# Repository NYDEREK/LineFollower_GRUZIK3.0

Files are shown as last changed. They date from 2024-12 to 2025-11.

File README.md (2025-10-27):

<h1 align="center">GRUZIK3.0: Line Follower Robot</h1>

<div align="center">

   

<i>Loved the project? Please consider giving a Star ⭐️</i>

</div>

> **GRUZIK2.0 is a lightweight construction (69g) designed for the "Line Follower Light" competition. The robot features Bluetooth communication with a smartphone app and uses a digital sensor instead of analog.**

> **here is a quick video of current progres with GRUZIK3.0 - https://www.youtube.com/watch?v=DpuIcFJMwbQ**
<div align="center">
  
</div>

## Hardware

> **The simple lightweight construction (69g) allows the robot to achieve high speed on the track.**
> **PCBs were designed in KiCAD 8.0 and manufactured by JLCPCB. The rims were 3D printed with PLA for Kyosho "Mini Z" tires.**
> **The light dualsky 150mAh battery provides enough current (max 30C) without adding too much weight (10g).**
> **The Pololu 2211 motor (10:1) with max current 1.6A per one requires the use of two separate TB6612FNG motor drivers with connected channels (max 2A per driver).**
> **The HC-05 Bluetooth module gives communication range up to 10m.**
> **The fast ARM microcontroller STM32G474RET6 (max 170MHz) provides a lot of software capabilities.**

- uC - STM32G474RET6
- drivers - TB6612FNG
- sensor - 12x KTIR0711S
- battery - 150mAh LiPo dualsky
- wheels - Kyosho Mini Z
- motors - Pololu 3071 HPCB
- Bluetooth - HC-04
- Encoders - AMS AS5047P-ATSM
- IMU - MPU-6050

## 🗺️ Mapping 🗺️
> **GRUZIK3.0 is able to record it's route and save it on uSD card. Results can be represented as XY map and optimized by Python algorithm, robot is able to recreate optimized map in real world achieving max speed for the given route**

<div align="center">

</div>

## 📱Bluetooth Apps 📱

> **Thease are simple Bluetooth apps created with MIT App Inventor. Spps start and stop the robot. The Modes pad is responsible for quickly adapting the speed and accuracy of the robot to the route using modes, and the application also displays the battery charge status. Second app is mainly for tweaking PID settings it allows you to change any parameter in seconds**

<div align="center">
  
  
</div>

## What I have learned 
> **This project wasn't easy but I learned a lot new things in software and hardware. I had a lot of failures during this project but I have never gave up and always kept pushing my own limits.**

- I mastered PID controll
 
- IMU implemantation 
 
- Encoder implementation with PI speed regulator on motors
 
- Mapping and optimizing Paths

- Improved my PCB design skills (KiCAD)

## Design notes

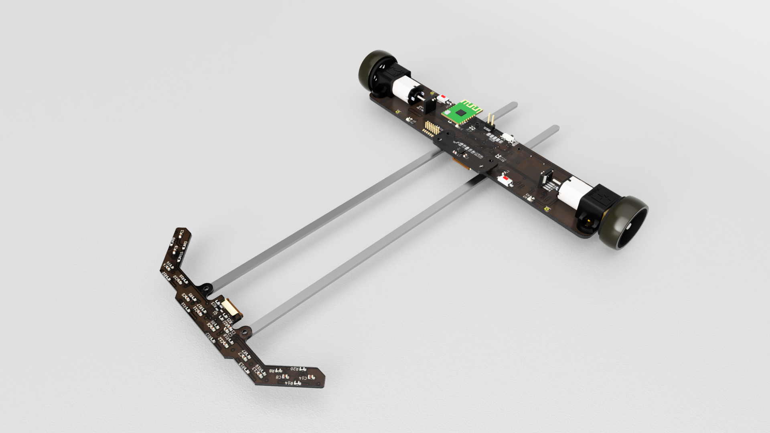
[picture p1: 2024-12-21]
Hardware/Renders/GRUZIK3.0_2024-Nov-24_09-44-59PM-000_CustomizedView13733252643_png.png

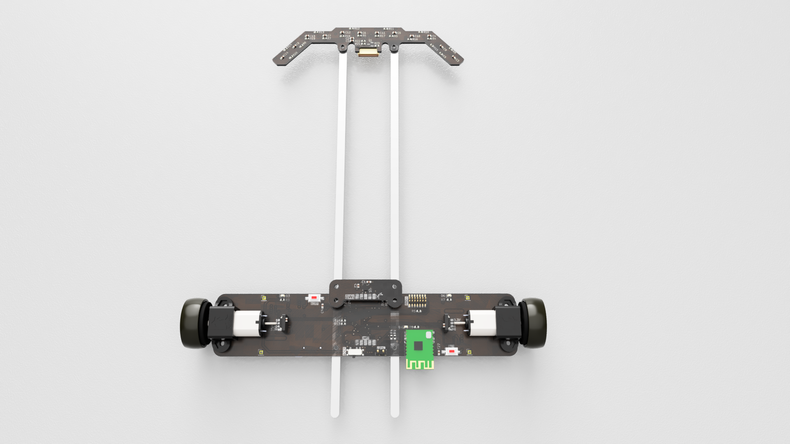
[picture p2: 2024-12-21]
Hardware/Renders/GRUZIK3.0_2024-Nov-24_10-15-36PM-000_CustomizedView15571638885_png.png

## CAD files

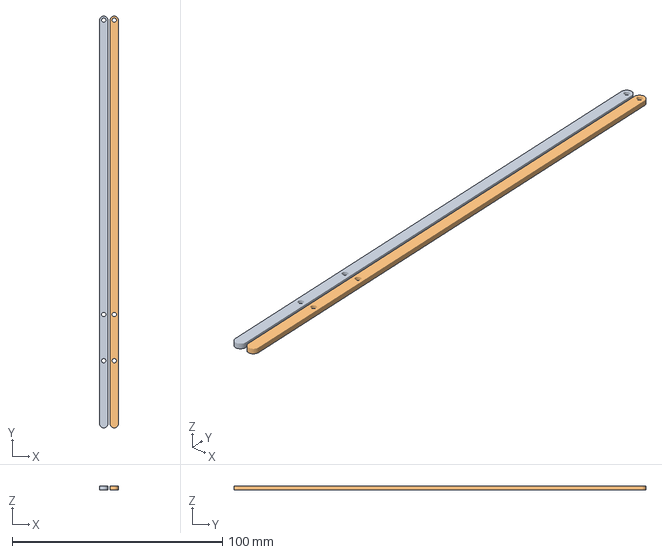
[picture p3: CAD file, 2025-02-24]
Hardware/3D Files/Board-Sensor-Connector/Connector.3mf
9.00 x 196.0 x 1.80 mm
Bryła1.stl x 2

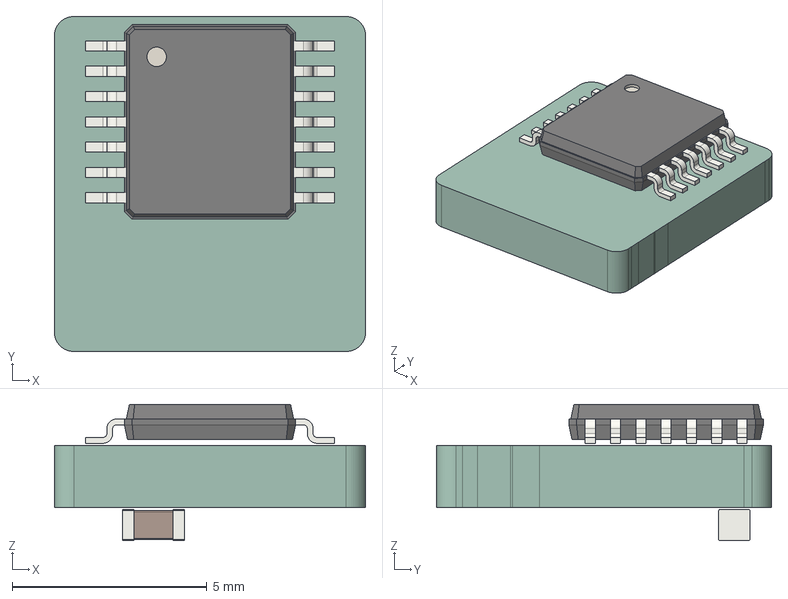
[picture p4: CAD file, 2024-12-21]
Hardware/3D Files/Encoder_3D_Files/Encoder_PCB.step
8.00 x 8.61 x 3.50 mm
TSSOP_14_44x5mm_P065mm
C_0603_1608Metric
Encoder_PCB_PCB

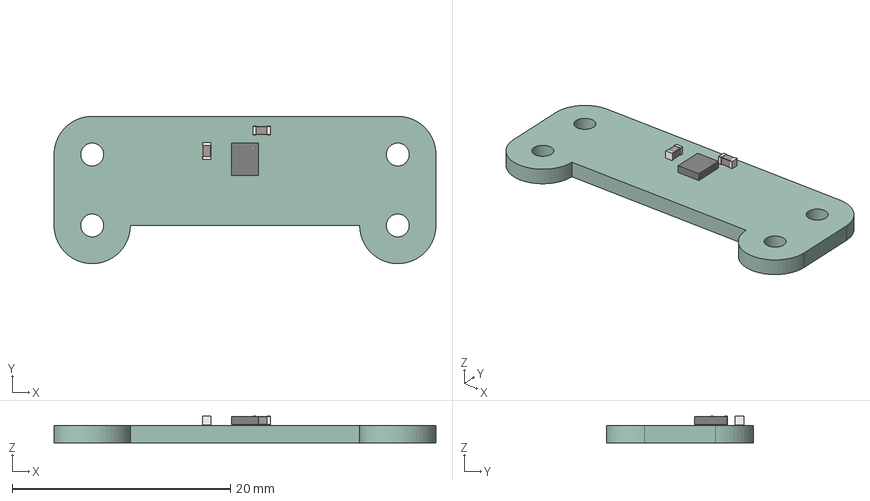
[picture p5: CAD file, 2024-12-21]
Hardware/3D Files/IMU_3D_Files/IMU_PCB.step
35.0 x 13.5 x 2.45 mm
LGA_14_3x25mm_P05mm_LayoutBorder3x4y
C_0603_1608Metric x 2
IMU_PCB_PCB

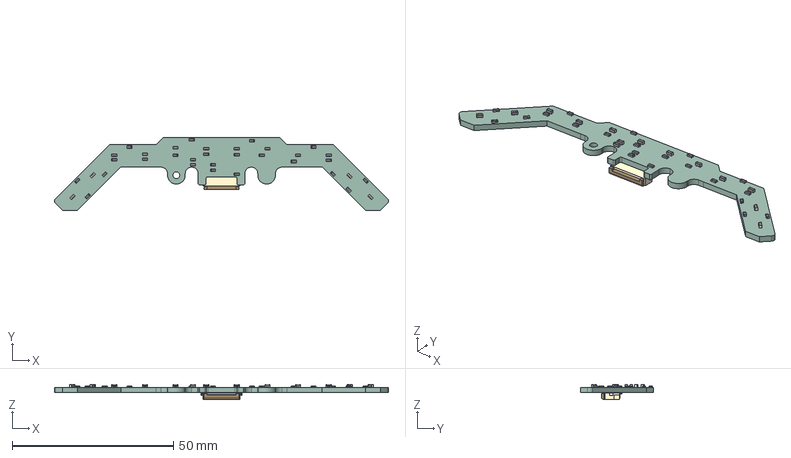
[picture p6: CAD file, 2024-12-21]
Hardware/3D Files/Sensor_3D_Files/Sensor_PCB.step
103.6 x 22.8 x 4.50 mm
C_0603_1608Metric x 14
R_0603_1608Metric x 21
Hirose_FH12_xxS_0_5SH_Parametric_v0_1
Sensor_PCB_PCB

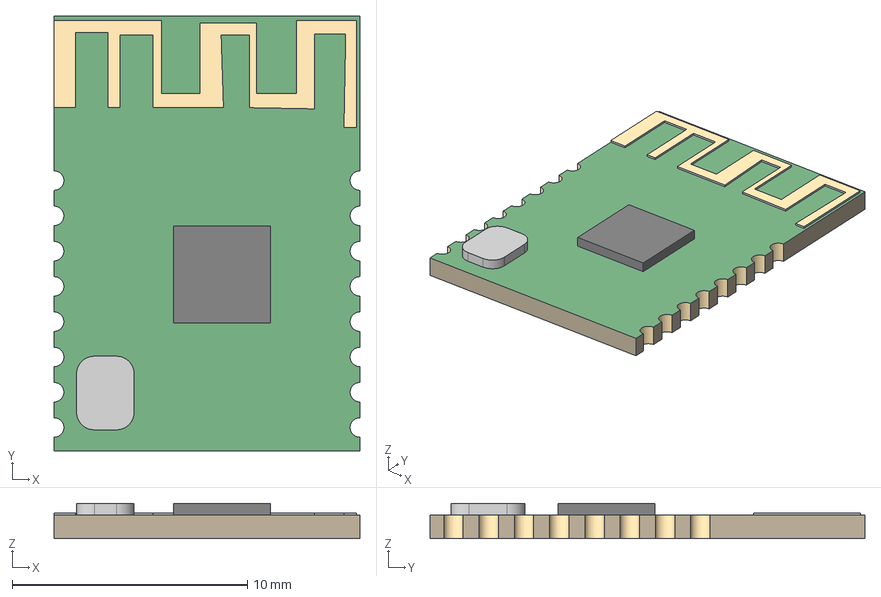
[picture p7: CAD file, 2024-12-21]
Hardware/PCB/KiCad project/Main_PCB_LF_3.0/Main_PCB_GRUZIK_3.0/HC-04/3D model/HC-04 v2.step
13.0 x 18.5 x 1.50 mm

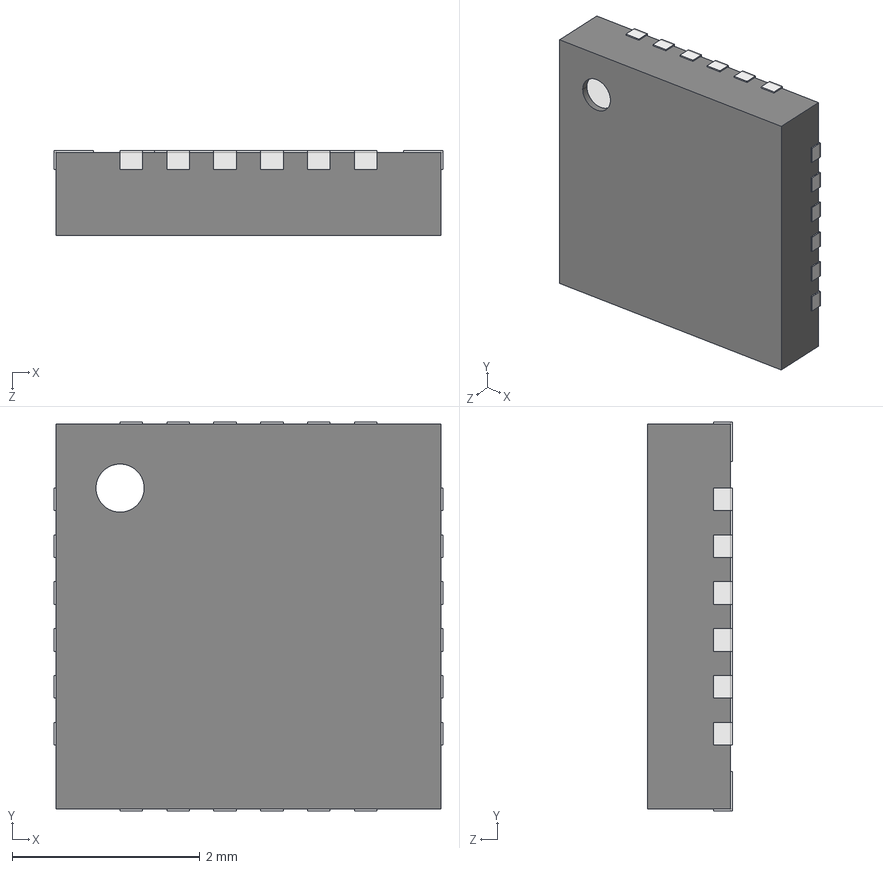
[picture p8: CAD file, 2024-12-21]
Hardware/PCB/KiCad project/Main_PCB_LF_3.0/Main_PCB_GRUZIK_3.0/MPU6050_3D_model/QFN 24.STEP
4.14 x 4.14 x 0.9 mm
Open_CASCADE_STEP_translator_6.8_11.2.1.step_Varsay考an
Open_CASCADE_STEP_translator_6.8_11.4.1.step_Varsay考an x 24
Open_CASCADE_STEP_translator_6.8_11.1.step_Varsay考an
Thermal_Shape.step_Varsay考an

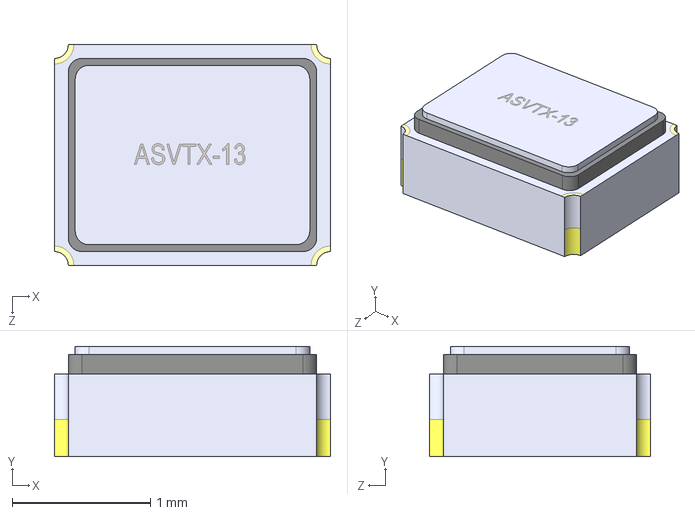
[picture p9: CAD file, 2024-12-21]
Hardware/PCB/KiCad project/Main_PCB_LF_3.0/Main_PCB_GRUZIK_3.0/X1_3D_model/ASVTX-13.STEP
2.00 x 0.8 x 1.60 mm

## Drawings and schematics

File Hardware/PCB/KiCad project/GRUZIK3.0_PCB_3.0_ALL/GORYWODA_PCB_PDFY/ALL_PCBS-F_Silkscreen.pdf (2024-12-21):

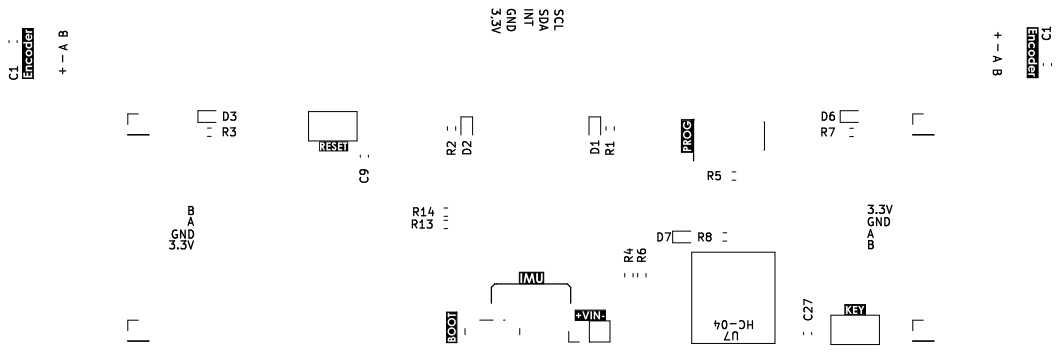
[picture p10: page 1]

GND SDA B B 3,3V INT SCL A GND AGND

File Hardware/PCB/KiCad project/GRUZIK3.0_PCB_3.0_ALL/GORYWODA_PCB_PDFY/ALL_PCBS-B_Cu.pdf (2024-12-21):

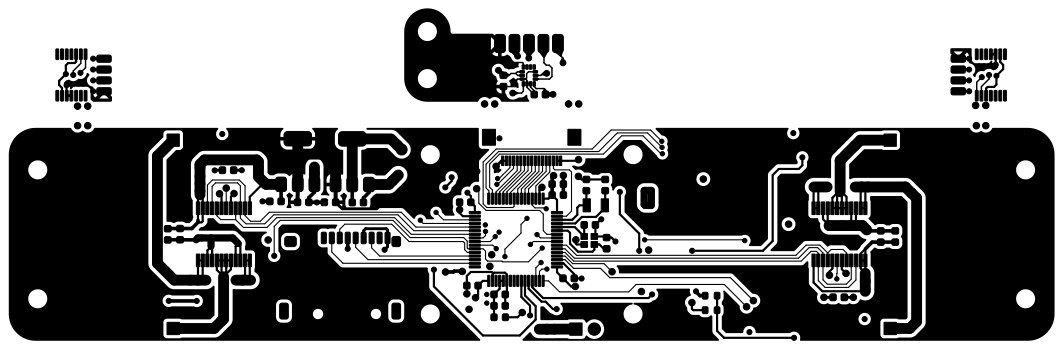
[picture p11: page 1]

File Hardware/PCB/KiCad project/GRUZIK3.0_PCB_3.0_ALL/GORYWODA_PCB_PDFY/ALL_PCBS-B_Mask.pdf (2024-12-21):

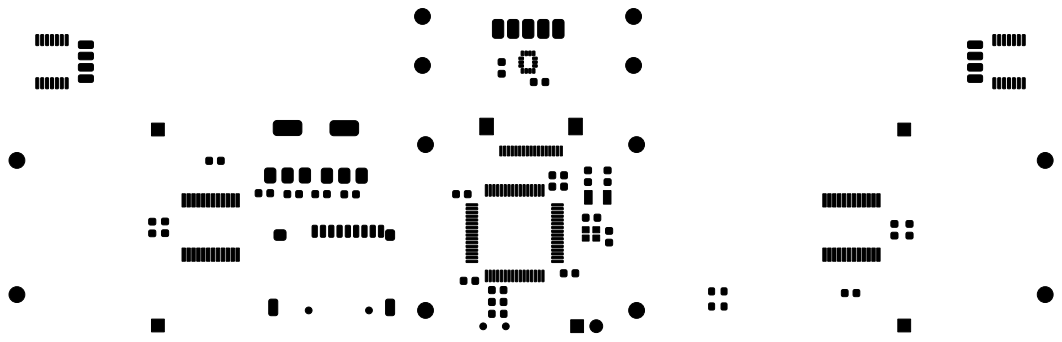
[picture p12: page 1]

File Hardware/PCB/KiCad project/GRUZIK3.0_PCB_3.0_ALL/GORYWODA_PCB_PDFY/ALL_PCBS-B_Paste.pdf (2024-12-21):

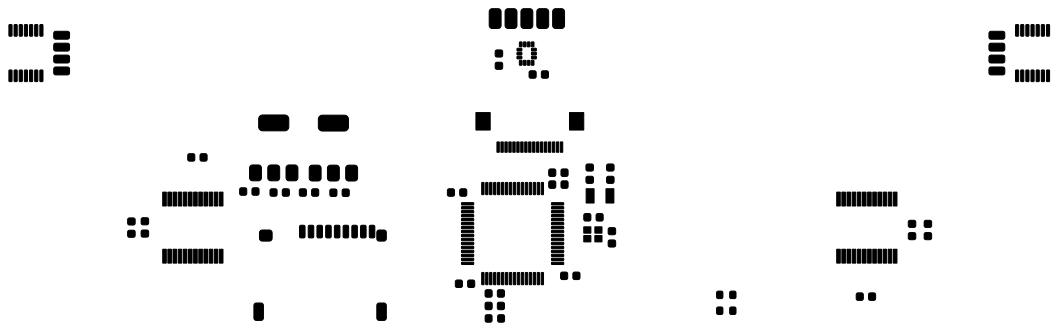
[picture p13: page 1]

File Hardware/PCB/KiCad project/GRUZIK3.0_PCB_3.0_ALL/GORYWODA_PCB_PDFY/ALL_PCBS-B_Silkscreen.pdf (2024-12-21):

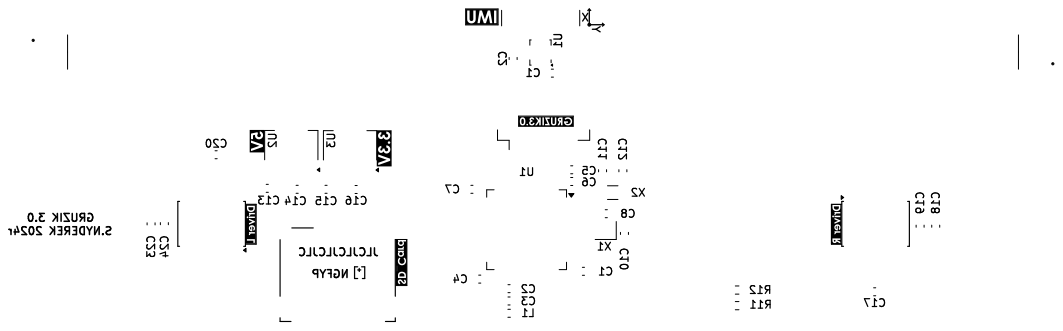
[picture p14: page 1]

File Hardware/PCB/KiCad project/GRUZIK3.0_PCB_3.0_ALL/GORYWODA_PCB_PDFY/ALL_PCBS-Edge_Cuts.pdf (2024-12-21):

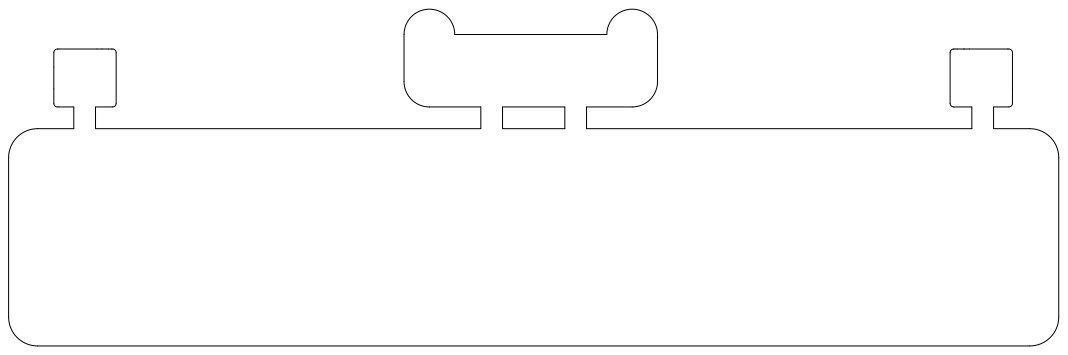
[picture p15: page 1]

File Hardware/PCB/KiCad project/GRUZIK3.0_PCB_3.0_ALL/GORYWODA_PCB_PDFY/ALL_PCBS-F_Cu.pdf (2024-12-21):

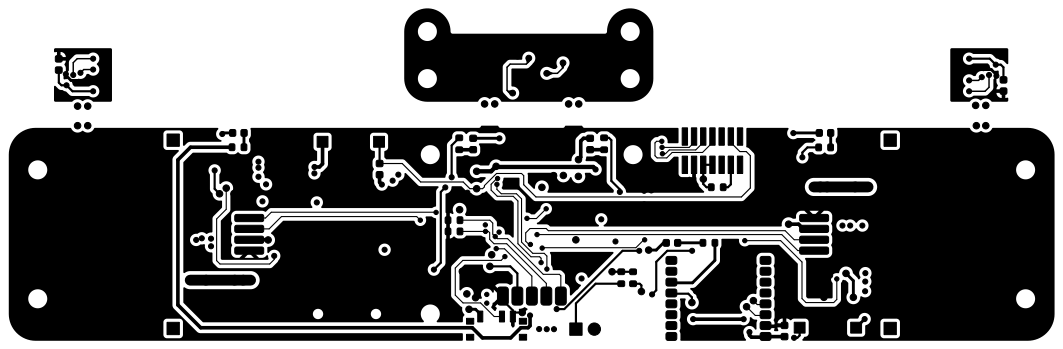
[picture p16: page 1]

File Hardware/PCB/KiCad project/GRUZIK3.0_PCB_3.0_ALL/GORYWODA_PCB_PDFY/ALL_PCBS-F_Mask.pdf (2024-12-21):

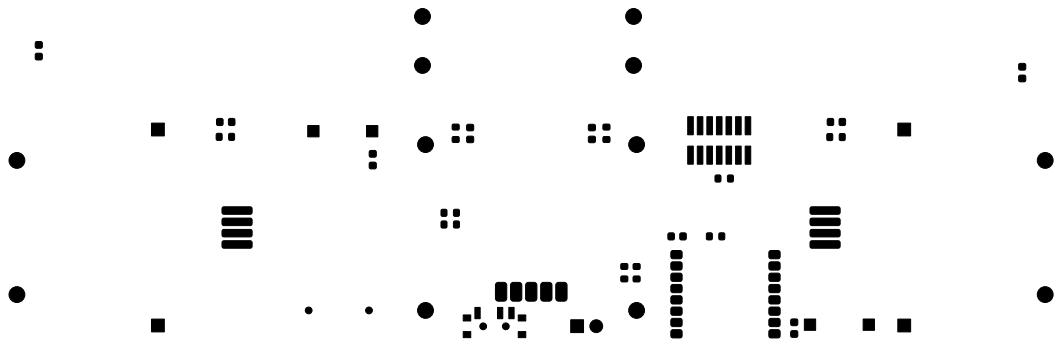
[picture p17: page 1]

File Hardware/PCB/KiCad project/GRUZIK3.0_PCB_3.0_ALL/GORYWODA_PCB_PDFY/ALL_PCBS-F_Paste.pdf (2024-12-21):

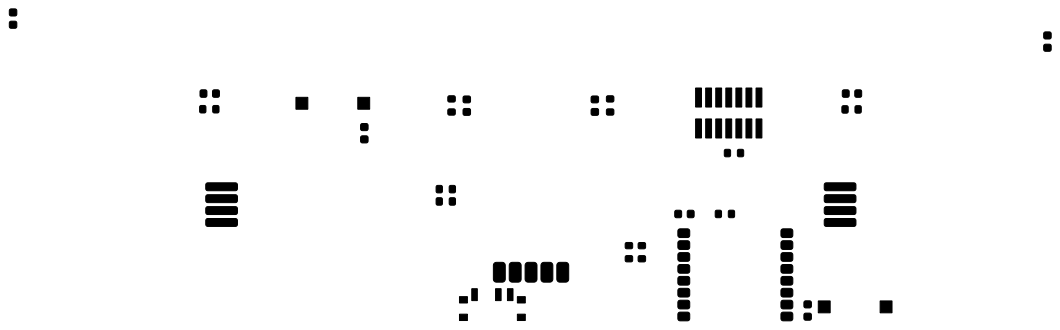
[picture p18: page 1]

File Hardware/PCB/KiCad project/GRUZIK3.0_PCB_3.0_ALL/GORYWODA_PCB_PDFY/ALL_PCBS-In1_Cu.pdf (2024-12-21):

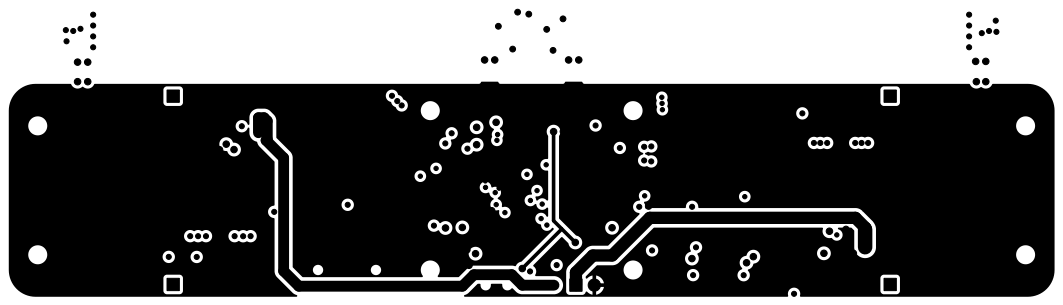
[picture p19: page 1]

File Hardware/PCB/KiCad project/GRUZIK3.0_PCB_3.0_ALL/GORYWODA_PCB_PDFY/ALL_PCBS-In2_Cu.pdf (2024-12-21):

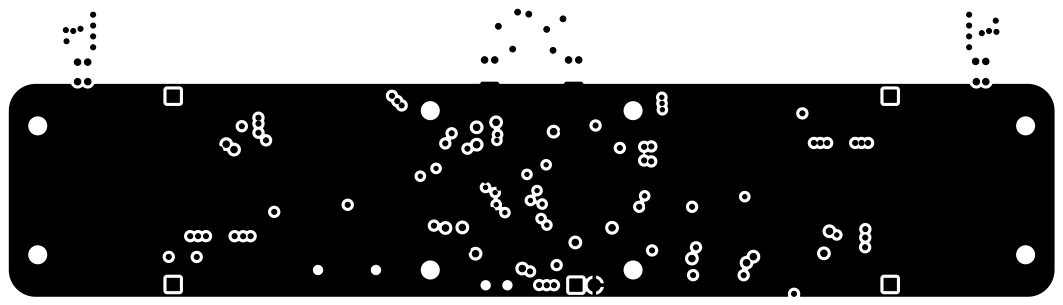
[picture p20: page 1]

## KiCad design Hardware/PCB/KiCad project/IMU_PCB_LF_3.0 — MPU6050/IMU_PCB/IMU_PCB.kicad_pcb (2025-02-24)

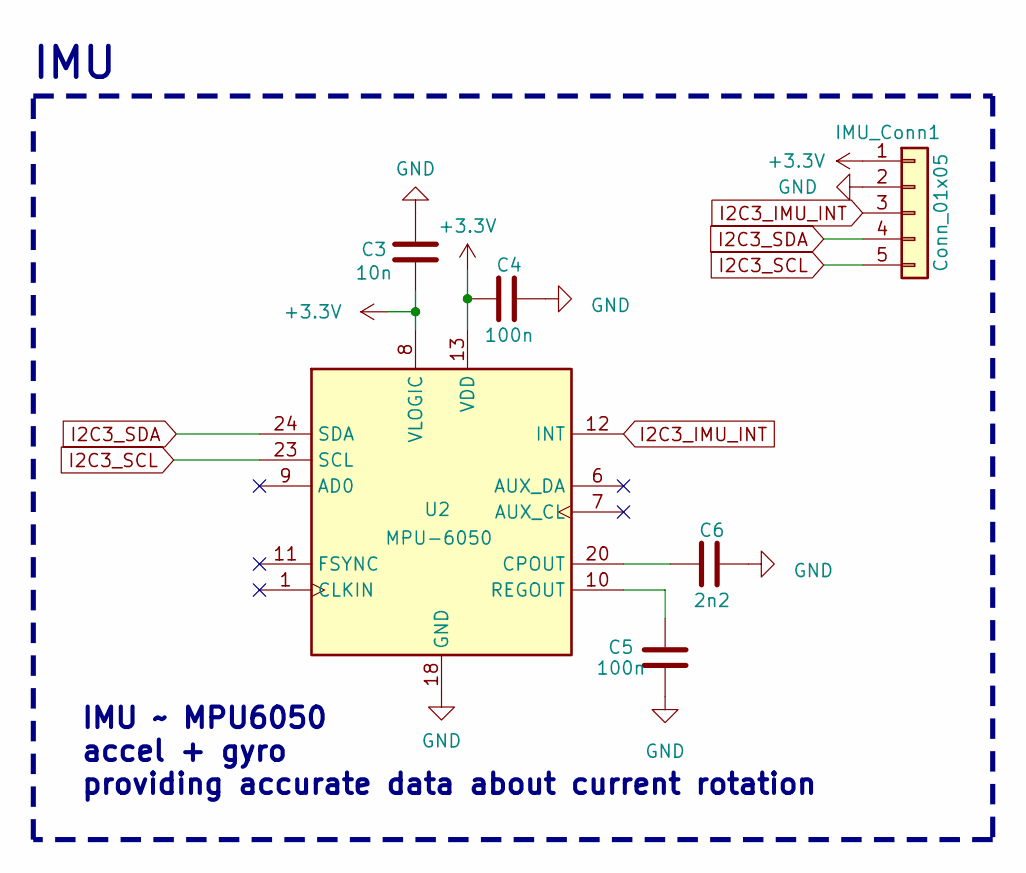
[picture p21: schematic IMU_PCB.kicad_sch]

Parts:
C3: 10n; C_0603_1608Metric
C4, C5: 100n; C_0603_1608Metric
C6: 2n2; C_0603_1608Metric
IMU_Conn1: Conn_01x05; IMU_conn
U2: MPU-6050; InvenSense_QFN-24_4x4mm_P0.5mm

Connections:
+3.3V: C3.1, C4.2, IMU_Conn1.1, U2.8 (VLOGIC), U2.13 (VDD)
GND: C3.2, C4.1, C5.2, C6.1, IMU_Conn1.2, U2.18 (GND)
I2C3_IMU_INT: IMU_Conn1.3, U2.12 (INT)
I2C3_SCL: IMU_Conn1.5, U2.23 (SCL)
I2C3_SDA: IMU_Conn1.4, U2.24 (SDA)
unnamed: C6.2, U2.20 (CPOUT)
unnamed: C5.1, U2.10 (REGOUT)

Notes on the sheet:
IMU
IMU ~ MPU6050 accel + gyro providing accurate data about current rotation

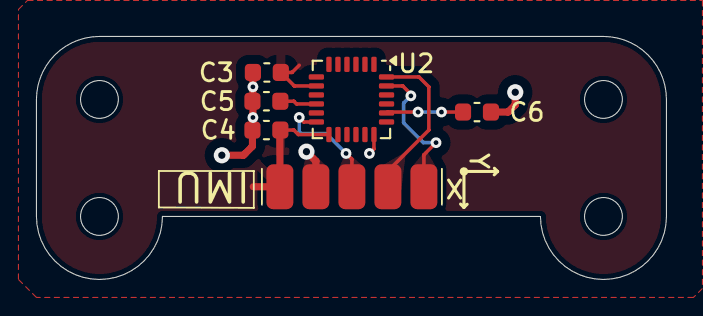
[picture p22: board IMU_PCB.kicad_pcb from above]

Board: 2 copper layers, 35.0 x 13.5 mm, 6 parts (0 on the bottom side), 7 nets.

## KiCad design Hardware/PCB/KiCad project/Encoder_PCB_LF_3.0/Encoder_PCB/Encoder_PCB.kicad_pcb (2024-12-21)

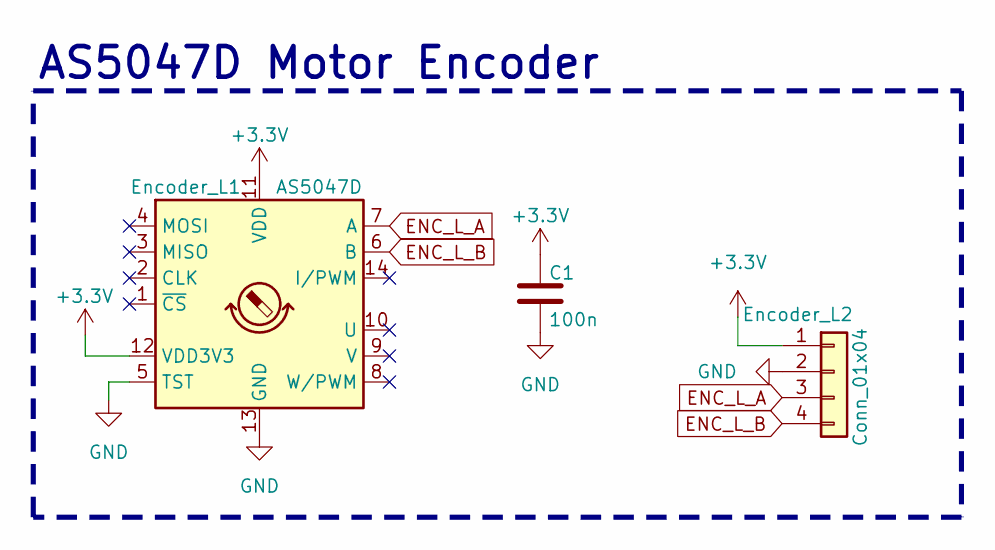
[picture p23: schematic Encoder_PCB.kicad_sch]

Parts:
C1: 100n; C_0603_1608Metric
Encoder_L1: AS5047D; TSSOP-14_4.4x5mm_P0.65mm
Encoder_L2: Conn_01x04; Encoder_short_conn

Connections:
+3.3V: C1.1, Encoder_L1.11 (VDD), Encoder_L1.12 (VDD3V3), Encoder_L2.1
ENC_L_A: Encoder_L1.7 (A), Encoder_L2.3
ENC_L_B: Encoder_L1.6 (B), Encoder_L2.4
GND: C1.2, Encoder_L1.5 (TST), Encoder_L1.13 (GND), Encoder_L2.2

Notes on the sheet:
AS5047D Motor Encoder

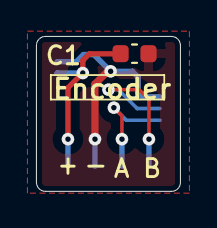
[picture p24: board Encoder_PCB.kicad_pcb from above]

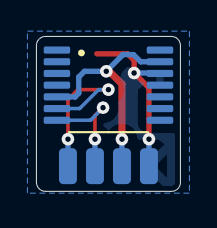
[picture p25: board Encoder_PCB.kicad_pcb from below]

Board: 2 copper layers, 8.0 x 8.6 mm, 3 parts (2 on the bottom side), 4 nets.

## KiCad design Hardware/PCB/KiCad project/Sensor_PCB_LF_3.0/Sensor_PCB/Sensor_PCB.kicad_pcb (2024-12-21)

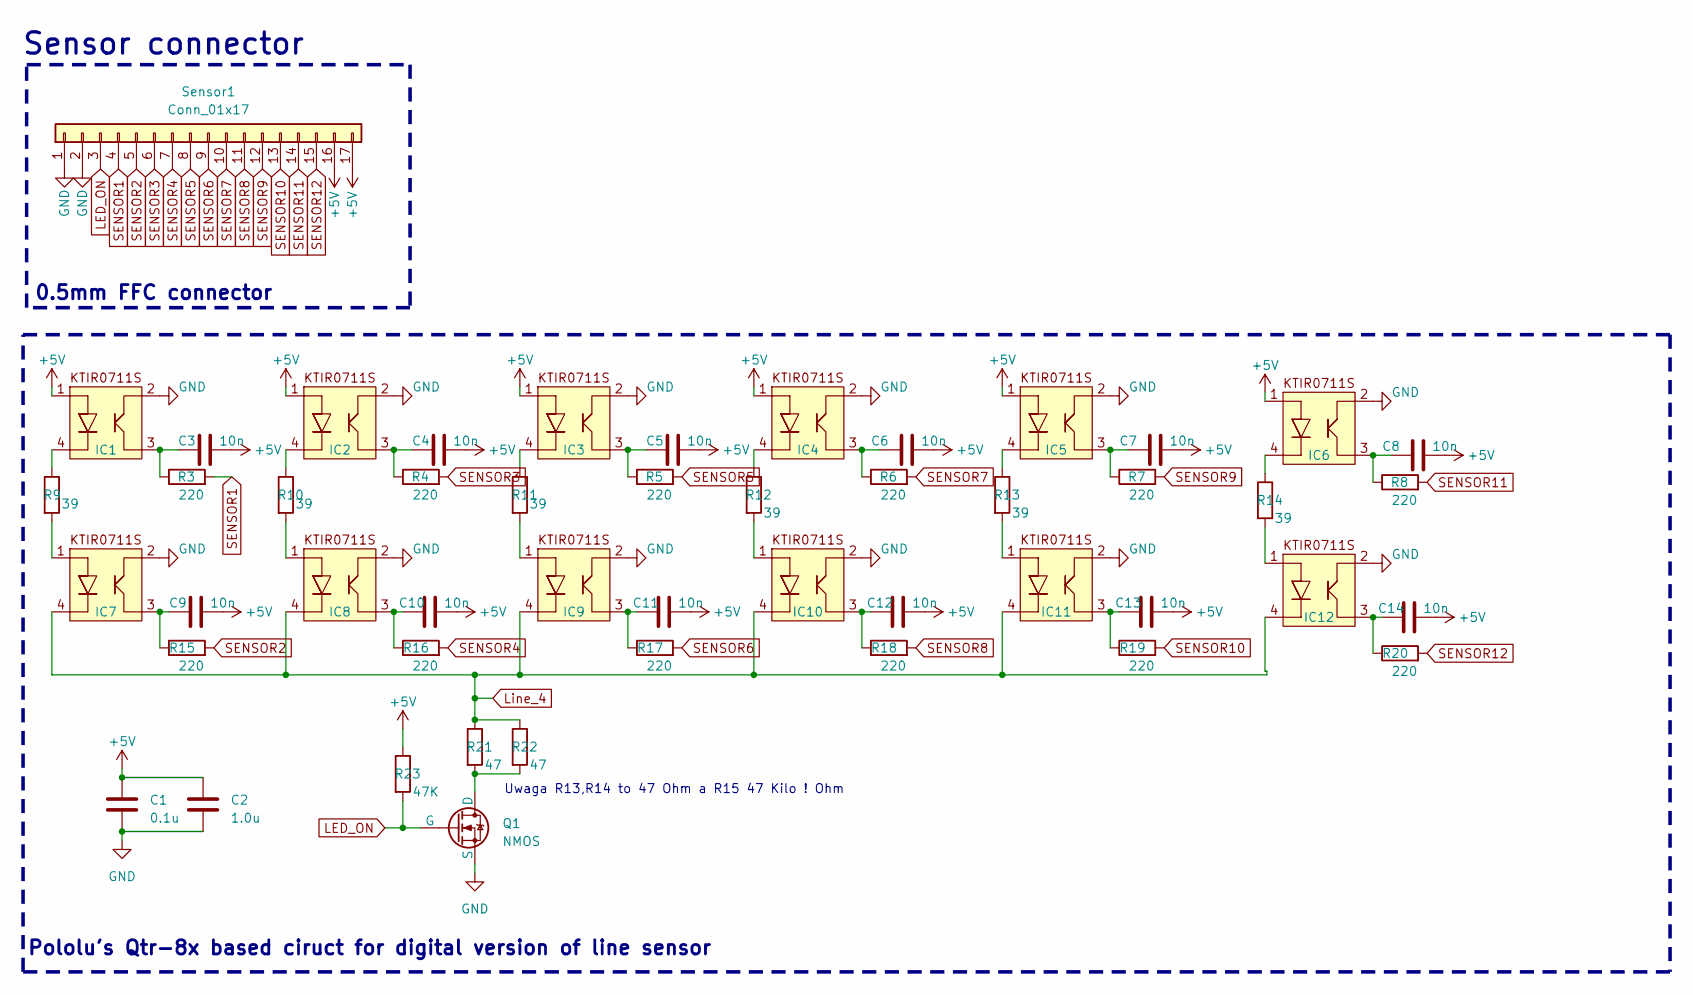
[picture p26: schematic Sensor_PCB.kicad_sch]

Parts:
C1: 0.1u; C_0603_1608Metric
C2: 1.0u; C_0603_1608Metric
C3, C4, C5, C6, C7, C8, C9, C10, C11, C12, C13, C14: 10n; C_0603_1608Metric
IC1, IC2, IC3, IC4, IC5, IC6, IC7, IC8, IC9, IC10, IC11, IC12: KTIR0711S
Q1: NMOS; NMOS_SN
R3, R4, R5, R6, R7, R8, R15, R16, R17, R18, R19, R20: 220; R_0603_1608Metric
R9, R10, R11, R12, R13, R14: 39; R_0603_1608Metric
R21, R22: 47; R_0603_1608Metric
R23: 47K; R_0603_1608Metric
Sensor1: Conn_01x17; Hirose_FH12-17S-0.5SH_1x17-1MP_P0.50mm_Horizontal

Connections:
+5V: C1.1, C2.1, C3.2, C4.2, C5.2, C6.2, C7.2, C8.2, C9.2, C10.2, C11.2, C12.2, C13.2, C14.2, IC1.1, IC2.1, IC3.1, IC4.1, IC5.1, IC6.1, R23.1, Sensor1.16, Sensor1.17; also elsewhere on the board
GND: C1.2, C2.2, IC1.2, IC2.2, IC3.2, IC4.2, IC5.2, IC6.2, IC7.2, IC8.2, IC9.2, IC10.2, IC11.2, IC12.2, Q1.3 (S), Sensor1.1, Sensor1.2; also elsewhere on the board
LED_ON: Q1.2 (G), R23.2, Sensor1.3; also elsewhere on the board
Line_4: IC7.4, IC8.4, IC9.4, IC10.4, IC11.4, IC12.4, R21.1, R22.1
unnamed: C3.1, IC1.3, R3.1
unnamed: C4.1, IC2.3, R4.1
unnamed: C5.1, IC3.3, R5.1
unnamed: C6.1, IC4.3, R6.1
unnamed: C7.1, IC5.3, R7.1
unnamed: C8.1, IC6.3, R8.1
unnamed: C9.1, IC7.3, R15.1
unnamed: C10.1, IC8.3, R16.1
unnamed: C11.1, IC9.3, R17.1
unnamed: C12.1, IC10.3, R18.1
unnamed: C13.1, IC11.3, R19.1
unnamed: C14.1, IC12.3, R20.1
unnamed: IC1.4, R9.1
unnamed: IC2.4, R10.1
unnamed: IC3.4, R11.1
unnamed: IC4.4, R12.1
unnamed: IC5.4, R13.1
unnamed: IC6.4, R14.1
unnamed: IC7.1, R9.2
unnamed: IC8.1, R10.2
unnamed: IC9.1, R11.2
unnamed: IC10.1, R12.2
unnamed: IC11.1, R13.2
unnamed: IC12.1, R14.2
unnamed: Q1.1 (D), R21.2, R22.2
SENSOR1: R3.2, Sensor1.4; also elsewhere on the board
SENSOR2: R15.2, Sensor1.5; also elsewhere on the board
SENSOR3: R4.2, Sensor1.6; also elsewhere on the board
SENSOR4: R16.2, Sensor1.7; also elsewhere on the board
SENSOR5: R5.2, Sensor1.8; also elsewhere on the board
SENSOR6: R17.2, Sensor1.9; also elsewhere on the board
SENSOR7: R6.2, Sensor1.10; also elsewhere on the board
SENSOR8: R18.2, Sensor1.11; also elsewhere on the board
SENSOR9: R7.2, Sensor1.12; also elsewhere on the board
SENSOR10: R19.2, Sensor1.13; also elsewhere on the board
SENSOR11: R8.2, Sensor1.14; also elsewhere on the board
SENSOR12: R20.2, Sensor1.15; also elsewhere on the board

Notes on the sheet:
Uwaga R13,R14 to 47 Ohm a R15 47 Kilo ! Ohm
Pololu's Qtr-8x based ciruct for digital version of line sensor
0.5mm FFC connector
Sensor connector

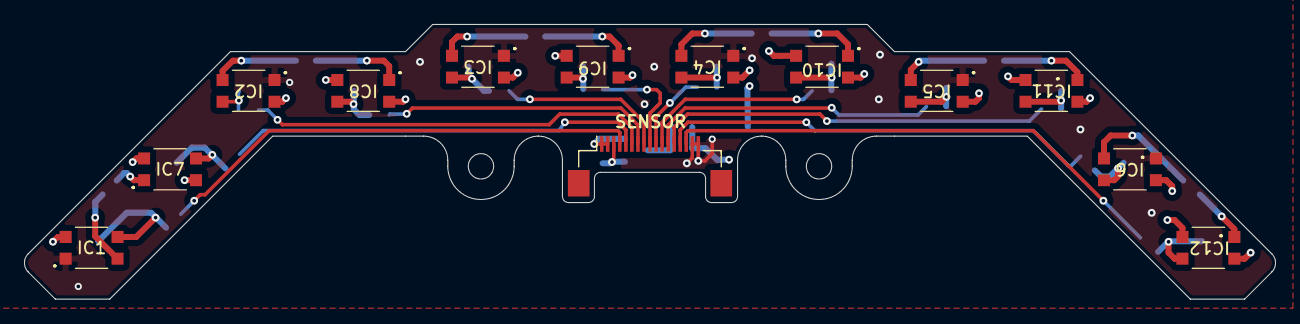
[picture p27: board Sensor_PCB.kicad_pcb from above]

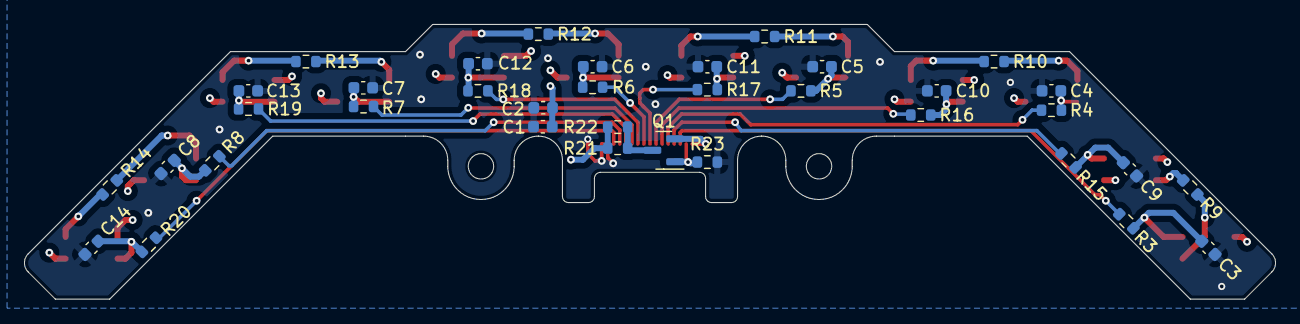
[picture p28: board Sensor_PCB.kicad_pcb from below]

Board: 4 copper layers, 103.6 x 22.8 mm, 49 parts (36 on the bottom side), 41 nets.

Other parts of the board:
SENSOR: Conn_01x17; Hirose_FH12-17S-0.5SH_1x17-1MP_P0.50mm_Horizontal

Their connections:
+5V: SENSOR.16, SENSOR.17; also elsewhere on the board
GND: SENSOR.1, SENSOR.2; also elsewhere on the board
LED_ON: SENSOR.3; also elsewhere on the board
SENSOR1: SENSOR.4; also elsewhere on the board
SENSOR2: SENSOR.5; also elsewhere on the board
SENSOR3: SENSOR.6; also elsewhere on the board
SENSOR4: SENSOR.7; also elsewhere on the board
SENSOR5: SENSOR.8; also elsewhere on the board
SENSOR6: SENSOR.9; also elsewhere on the board
SENSOR7: SENSOR.10; also elsewhere on the board
SENSOR8: SENSOR.11; also elsewhere on the board
SENSOR9: SENSOR.12; also elsewhere on the board
SENSOR10: SENSOR.13; also elsewhere on the board
SENSOR11: SENSOR.14; also elsewhere on the board
SENSOR12: SENSOR.15; also elsewhere on the board

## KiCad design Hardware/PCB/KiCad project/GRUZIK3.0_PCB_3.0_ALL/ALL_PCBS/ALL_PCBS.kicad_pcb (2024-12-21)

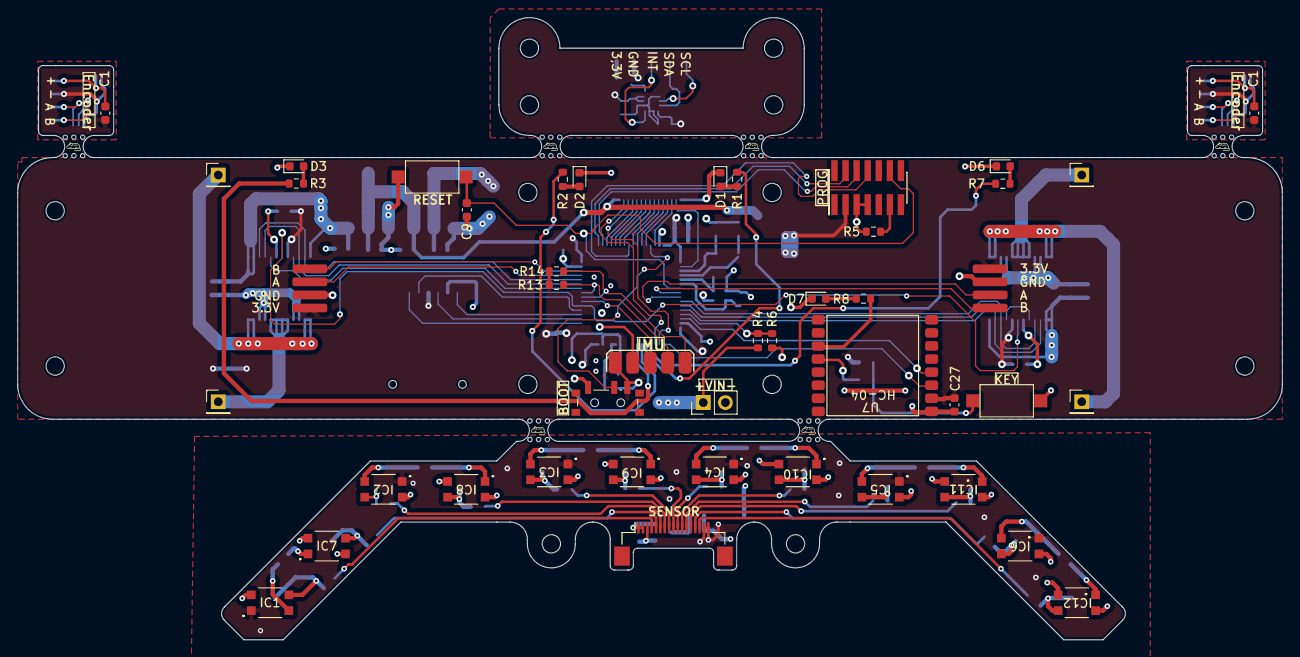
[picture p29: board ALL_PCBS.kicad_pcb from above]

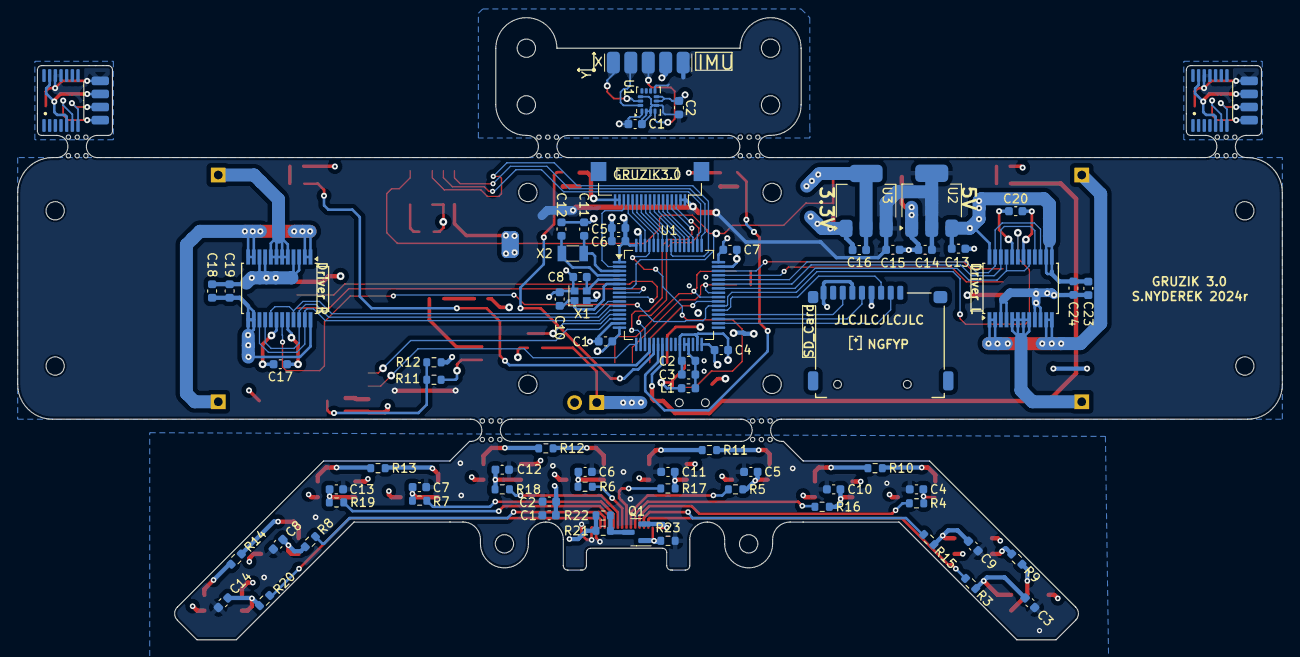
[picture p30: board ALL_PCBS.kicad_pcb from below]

Board: 4 copper layers, 145.0 x 71.3 mm, 128 parts (77 on the bottom side), 92 nets.

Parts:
+VIN-: +VIN-; PinHeader_1x02_P2.54mm_Vertical
BOOT: SW_DPDT_x2; SW_SPDT_PCM12
C1, C1#2, C1#3, C1#4, C2, C2#2, C5, C6#2, C7#2, C9, C17, C18, C20, C23: 100n; C_0603_1608Metric
C1#5: 0.1u; C_0603_1608Metric
C2#3: 1.0u; C_0603_1608Metric
C3, C27: 1u; C_0603_1608Metric
C3#2, C4, C5#2, C6, C7, C8, C9#2, C10#2, C11#2, C12, C13, C14: 10n; C_0603_1608Metric
C4#2: 4u7; C_0603_1608Metric
C8#2, C10: 6p8; C_0603_1608Metric
C11, C12#2: 5p1; C_0603_1608Metric
C13#2, C14#2, C15, C16, C19, C24: 10u; C_0603_1608Metric
D1, D2, D3, D6: BLUE; LED_0603_1608Metric
D7: Green; LED_0603_1608Metric
Driver L: TB6612FNG; SSOP-24_5.3x8.2mm_P0.65mm
Driver R: TB6612FNG; SSOP-24_5.3x8.2mm_P0.65mm
Encoder_L1, Encoder_L2, Encoder_L2#2, Encoder_L2#3: Conn_01x04; Encoder_short_conn
Encoder_L1#2, Encoder_L1#3: AS5047D; TSSOP-14_4.4x5mm_P0.65mm
GRUZIK3.0: Conn_01x17; Hirose_FH12-17S-0.5SH_1x17-1MP_P0.50mm_Horizontal
IC1, IC2, IC3, IC4, IC5, IC6, IC7, IC8, IC9, IC10, IC11, IC12: KTIR0711S
IMU: Conn_01x05; IMU_conn
IMU_Conn1: Conn_01x05; IMU_conn
KEY: SW_SPST; SW_SPST_CK_RS282G05A3
L1: 27n; L_0603_1608Metric
P1, P2, P3, P4: Conn_01x01; PinHeader_1x01_P2.54mm_Vertical
PROG: Conn_02x07_Odd_Even; PinHeader_2x07_P1.27mm_Vertical_SMD
Q1: NMOS; NMOS_SN
R1, R2, R3, R7: 510R; R_0603_1608Metric
R3#2, R4#2, R5#2, R6#2, R7#2, R8#2, R11#2, R15, R16, R17, R18, R19, R20: 220; R_0603_1608Metric
R4: 330K; R_0603_1608Metric
R5: 100R; R_0603_1608Metric
R6: 200K; R_0603_1608Metric
R8: 510; R_0603_1608Metric
R9, R10, R11, R12#2, R13#2, R14#2: 39; R_0603_1608Metric
R12, R13, R14: 10K; R_0603_1608Metric
R21, R22: 47; R_0603_1608Metric
R23: 47K; R_0603_1608Metric
RESET: SW_SPST; SW_SPST_CK_RS282G05A3
SD_Card: Micro_SD_Card; micro_SD
SENSOR: Conn_01x17; Hirose_FH12-17S-0.5SH_1x17-1MP_P0.50mm_Horizontal
U1: LSM6DS3; LGA-14_3x2.5mm_P0.5mm_LayoutBorder3x4y
U1#2: STM32G474RETx; LQFP-64_10x10mm_P0.5mm
U2: AMS1117-5.0; SOT-223-3_TabPin2
U3: AMS1117-3.3; SOT-223-3_TabPin2
U7: HC-04
X1: 24Mhz; Crystal_SMD_2016-4Pin_2.0x1.6mm
X2: 32.768KHz; Crystal_SMD_3215-2Pin_3.2x1.5mm
mouse-bite-2.54mm-4.66mm, mouse-bite-2.54mm-4.66mm#2, mouse-bite-2.54mm-4.66mm#3, mouse-bite-2.54mm-4.66mm#4, mouse-bite-2.54mm-4.66mm#5, mouse-bite-2.54mm-4.66mm#6: VAL**; mouse-bite-2.54mm-4.66mm

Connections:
+3.3V: C1.1, C1#2.1, C1#3.1, C2#2.2, Encoder_L1#2.11 (VDD), Encoder_L1#2.12 (VDD3V3), Encoder_L1#3.11 (VDD), Encoder_L1#3.12 (VDD3V3), Encoder_L2#2.1, Encoder_L2#3.1, IMU_Conn1.1, U1.2 (SDX), U1.3 (SCX), U1.5 (VDDIO), U1.8 (VDD), U1.12 (CS)
+3V3: BOOT.3 (C), C1#4.1, C4#2.1, C5.1, C6#2.1, C7#2.1, C16.1, C17.1, C20.1, C27.1, Driver L.20 (VCC), Driver R.20 (VCC), Encoder_L1.1, Encoder_L2.1, IMU.1, L1.2, PROG.3, R12.2, R13.1, R14.1, SD_Card.4 (VDD), U1#2.1 (VBAT), U1#2.16 (VDD), U1#2.32 (VDD), U1#2.48 (VDD), U1#2.64 (VDD), U3.2 (VO), U7.2 (3.3V)
+5V: C1#5.1, C2#3.1, C3#2.2, C4.2, C5#2.2, C6.2, C7.2, C8.2, C9#2.2, C10#2.2, C11#2.2, C12.2, C13.2, C14.2, C14#2.1, C15.1, GRUZIK3.0.1, GRUZIK3.0.2, IC1.1, IC2.1, IC3.1, IC4.1, IC5.1, IC6.1, R23.1, SENSOR.16, SENSOR.17, U2.2 (VO), U3.3 (VI)
/HSE_IN: C8#2.2, U1#2.5 (PF0), X1.3
/HSE_OUT: C10.2, U1#2.6 (PF1), X1.1
/LSE_IN: C11.2, U1#2.3 (PC14), X2.2
/LSE_OUT: C12#2.2, U1#2.4 (PC15), X2.1
ADC_IN2: R4.1, R6.2, U1#2.13 (PA1)
BOOT0: BOOT.2 (B), U1#2.61 (PB8)
ENC_L_A: Encoder_L1.3, Encoder_L1#2.7 (A), Encoder_L1#3.7 (A), Encoder_L2#2.3, Encoder_L2#3.3, U1#2.45 (PA11)
ENC_L_B: Encoder_L1.4, Encoder_L1#2.6 (B), Encoder_L1#3.6 (B), Encoder_L2#2.4, Encoder_L2#3.4, U1#2.46 (PA12)
ENC_R_A: Encoder_L2.3, U1#2.9 (PC1)
ENC_R_B: Encoder_L2.4, U1#2.8 (PC0)
GND: +VIN-.2, BOOT.1 (A), C1.2, C1#2.2, C1#3.2, C1#4.2, C1#5.2, C2.2, C2#2.1, C2#3.2, C3.2, C4#2.2, C5.2, C6#2.2, C7#2.2, C8#2.1, C9.1, C10.1, C11.1, C12#2.1, C13#2.2, C14#2.2, C15.2, C16.2, C17.2, C18.2, C19.2, C20.2, C23.2, C24.2, C27.2, D1.1 (K), D2.1 (K), D3.1 (K), D6.1 (K), D7.1 (K), Driver L.3 (PGND1), Driver L.4 (PGND1), Driver L.9 (PGND2), Driver L.10 (PGND2), Driver L.18 (GND), Driver R.3 (PGND1), Driver R.4 (PGND1), Driver R.9 (PGND2), Driver R.10 (PGND2), Driver R.18 (GND), Encoder_L1.2, Encoder_L1#2.5 (TST), Encoder_L1#2.13 (GND), Encoder_L1#3.5 (TST), Encoder_L1#3.13 (GND), Encoder_L2.2, Encoder_L2#2.2, Encoder_L2#3.2, GRUZIK3.0.16, GRUZIK3.0.17, IC1.2, IC2.2, IC3.2, IC4.2, IC5.2, IC6.2, IC7.2, IC8.2, IC9.2, IC10.2, IC11.2, IC12.2, IMU.2, IMU_Conn1.2, KEY.2 (B), PROG.5, PROG.7, Q1.3 (S), R5.1, R6.1, RESET.1 (A), SD_Card.6 (VSS), SD_Card.9 (SHIELD), SENSOR.1, SENSOR.2, U1.1 (SDO/SA0), U1.6 (GND), U1.7 (GND), U1#2.15 (VSS), U1#2.27 (VSSA), U1#2.31 (VSS), U1#2.47 (VSS), U1#2.63 (VSS), U2.1 (GND), U3.1 (GND), U7.1 (GND), X1.2, X1.4
I2C3_IMU_INT: IMU.3, IMU_Conn1.3, U1.4 (INT1), U1#2.39 (PC7)
I2C3_SCL: IMU.5, IMU_Conn1.5, R14.2, U1.13 (SCL), U1#2.40 (PC8)
I2C3_SDA: IMU.4, IMU_Conn1.4, R13.2, U1.14 (SDA), U1#2.41 (PC9)
LED_1: R3.2, U1#2.23 (PC5)
LED_2: R2.2, U1#2.22 (PC4)
LED_3: R1.2, U1#2.21 (PA7)
LED_4: R7.2, U1#2.20 (PA6)
LED_ON: GRUZIK3.0.15, Q1.2 (G), R23.2, SENSOR.3, U1#2.2 (PC13)
LPUART1_RX: U1#2.17 (PA3), U7.3 (Tx)
LPUART1_TX: U1#2.14 (PA2), U7.4 (Rx)
Line_4: IC7.4, IC8.4, IC9.4, IC10.4, IC11.4, IC12.4, R21.1, R22.1
Motor_L_A: Driver L.17 (BIN1), Driver L.21 (AIN1), U1#2.42 (PA8)
Motor_L_B: Driver L.16 (BIN2), Driver L.22 (AIN2), U1#2.43 (PA9)
Motor_R_A: Driver R.17 (BIN1), Driver R.21 (AIN1), U1#2.10 (PC2)
Motor_R_B: Driver R.16 (BIN2), Driver R.22 (AIN2), U1#2.11 (PC3)
Motor_STBY: Driver L.19 (STBY), Driver R.19 (STBY), U1#2.38 (PC6)
NRST: C9.2, PROG.12, RESET.2 (B), U1#2.7 (PG10)
unnamed: C3#2.1, IC1.3, R3#2.1
unnamed: C4.1, IC2.3, R4#2.1
unnamed: C5#2.1, IC3.3, R5#2.1
unnamed: C6.1, IC4.3, R6#2.1
unnamed: C7.1, IC5.3, R7#2.1
unnamed: C8.1, IC6.3, R8#2.1
unnamed: C9#2.1, IC7.3, R15.1
unnamed: C10#2.1, IC8.3, R16.1
unnamed: C11#2.1, IC9.3, R17.1
unnamed: C12.1, IC10.3, R18.1
unnamed: C13.1, IC11.3, R19.1
unnamed: C14.1, IC12.3, R20.1
unnamed: D1.2 (A), R1.1
unnamed: D2.2 (A), R2.1
unnamed: D3.2 (A), R3.1
unnamed: D6.2 (A), R7.1
unnamed: D7.2 (A), R8.2
unnamed: IC1.4, R9.1
unnamed: IC2.4, R10.1
unnamed: IC3.4, R11.1
unnamed: IC4.4, R12#2.1
unnamed: IC5.4, R13#2.1
unnamed: IC6.4, R14#2.1
unnamed: IC7.1, R9.2
unnamed: IC8.1, R10.2
unnamed: IC9.1, R11.2
unnamed: IC10.1, R12#2.2
unnamed: IC11.1, R13#2.2
unnamed: IC12.1, R14#2.2
unnamed: KEY.1 (A), R11#2.2, R12.1
unnamed: Driver R.5 (AO2), Driver R.6 (AO2), Driver R.7 (BO2), Driver R.8 (BO2), P1.1
unnamed: Driver R.1 (AO1), Driver R.2 (AO1), Driver R.11 (BO1), Driver R.12 (BO1), P2.1
unnamed: Driver L.5 (AO2), Driver L.6 (AO2), Driver L.7 (BO2), Driver L.8 (BO2), P3.1
unnamed: Driver L.1 (AO1), Driver L.2 (AO1), Driver L.11 (BO1), Driver L.12 (BO1), P4.1
unnamed: PROG.11, R5.2
unnamed: Q1.1 (D), R21.2, R22.2
unnamed: R11#2.1, U7.12 (KEY)
unnamed: R8.1, U7.11 (LED)
PWM_L: Driver L.15 (PWMB), Driver L.23 (PWMA), U1#2.44 (PA10)
PWM_R: Driver R.15 (PWMB), Driver R.23 (PWMA), U1#2.12 (PA0)
SENSOR1: GRUZIK3.0.14, R3#2.2, SENSOR.4, U1#2.62 (PB9)
SENSOR2: GRUZIK3.0.13, R15.2, SENSOR.5, U1#2.60 (PB7)
SENSOR3: GRUZIK3.0.12, R4#2.2, SENSOR.6, U1#2.59 (PB6)
SENSOR4: GRUZIK3.0.11, R16.2, SENSOR.7, U1#2.58 (PB5)
SENSOR5: GRUZIK3.0.10, R5#2.2, SENSOR.8, U1#2.57 (PB4)
SENSOR6: GRUZIK3.0.9, R17.2, SENSOR.9, U1#2.55 (PD2)
SENSOR7: GRUZIK3.0.8, R6#2.2, SENSOR.10, U1#2.54 (PC12)
SENSOR8: GRUZIK3.0.7, R18.2, SENSOR.11, U1#2.53 (PC11)
SENSOR9: GRUZIK3.0.6, R7#2.2, SENSOR.12, U1#2.52 (PC10)
SENSOR10: GRUZIK3.0.5, R19.2, SENSOR.13, U1#2.51 (PA15)
SENSOR11: GRUZIK3.0.4, R8#2.2, SENSOR.14, U1#2.18 (PA4)
SENSOR12: GRUZIK3.0.3, R20.2, SENSOR.15, U1#2.19 (PA5)
SPI2_CLK: SD_Card.5 (CLK), U1#2.35 (PB13)
SPI2_CS: SD_Card.2 (DAT3/CD), U1#2.34 (PB12)
SPI2_MISO: SD_Card.7 (DAT0), U1#2.36 (PB14)
SPI2_MOSI: SD_Card.3 (CMD), U1#2.37 (PB15)
SYS_JTCK_SWCLK: PROG.6, U1#2.50 (PA14)
SYS_JTDO_SWO: PROG.8, U1#2.56 (PB3)
SYS_JTMS_SWDIO: PROG.4, U1#2.49 (PA13)
VDC: +VIN-.1, C13#2.1, C18.1, C19.1, C23.1, C24.1, Driver L.13 (VM2), Driver L.14 (VM3), Driver L.24 (VM1), Driver R.13 (VM2), Driver R.14 (VM3), Driver R.24 (VM1), R4.2, U2.3 (VI)
VREF+: C2.1, C3.1, L1.1, U1#2.28 (VREF+), U1#2.29 (VDDA)

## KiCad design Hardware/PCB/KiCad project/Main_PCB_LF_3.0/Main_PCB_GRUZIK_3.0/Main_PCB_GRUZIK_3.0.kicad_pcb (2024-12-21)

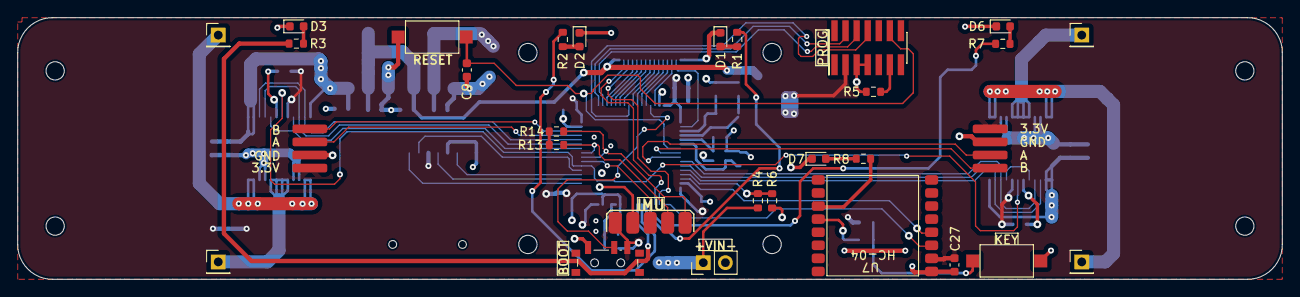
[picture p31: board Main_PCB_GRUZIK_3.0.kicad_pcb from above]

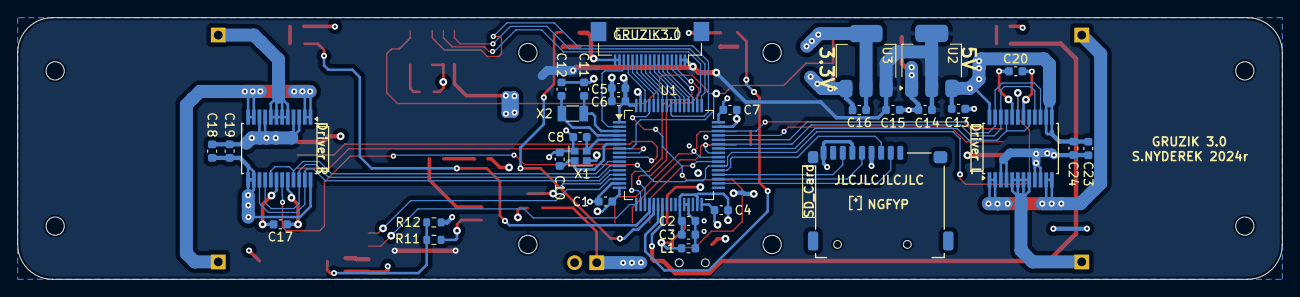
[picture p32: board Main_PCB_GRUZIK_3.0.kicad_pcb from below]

Board: 4 copper layers, 145.0 x 30.0 mm, 63 parts (33 on the bottom side), 65 nets.

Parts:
+VIN-: +VIN-; PinHeader_1x02_P2.54mm_Vertical
BOOT: SW_DPDT_x2; SW_SPDT_PCM12
C1, C2, C5, C6, C7, C9, C17, C18, C20, C23: 100n; C_0603_1608Metric
C3, C27: 1u; C_0603_1608Metric
C4: 4u7; C_0603_1608Metric
C8, C10: 6p8; C_0603_1608Metric
C11, C12: 5p1; C_0603_1608Metric
C13, C14, C15, C16, C19, C24: 10u; C_0603_1608Metric
D1, D2, D3, D6: BLUE; LED_0603_1608Metric
D7: Green; LED_0603_1608Metric
Driver L: TB6612FNG; SSOP-24_5.3x8.2mm_P0.65mm
Driver R: TB6612FNG; SSOP-24_5.3x8.2mm_P0.65mm
Encoder_L1, Encoder_L2: Conn_01x04; Encoder_short_conn
GRUZIK3.0: Conn_01x17; Hirose_FH12-17S-0.5SH_1x17-1MP_P0.50mm_Horizontal
IMU: Conn_01x05; IMU_conn
KEY: SW_SPST; SW_SPST_CK_RS282G05A3
L1: 27n; L_0603_1608Metric
P1, P2, P3, P4: Conn_01x01; PinHeader_1x01_P2.54mm_Vertical
PROG: Conn_02x07_Odd_Even; PinHeader_2x07_P1.27mm_Vertical_SMD
R1, R2, R3, R7: 510R; R_0603_1608Metric
R4: 330K; R_0603_1608Metric
R5: 100R; R_0603_1608Metric
R6: 200K; R_0603_1608Metric
R8: 510; R_0603_1608Metric
R11: 220; R_0603_1608Metric
R12, R13, R14: 10K; R_0603_1608Metric
RESET: SW_SPST; SW_SPST_CK_RS282G05A3
SD_Card: Micro_SD_Card; micro_SD
U1: STM32G474RETx; LQFP-64_10x10mm_P0.5mm
U2: AMS1117-5.0; SOT-223-3_TabPin2
U3: AMS1117-3.3; SOT-223-3_TabPin2
U7: HC-04
X1: 24Mhz; Crystal_SMD_2016-4Pin_2.0x1.6mm
X2: 32.768KHz; Crystal_SMD_3215-2Pin_3.2x1.5mm

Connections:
+3V3: BOOT.3 (C), C1.1, C4.1, C5.1, C6.1, C7.1, C16.1, C17.1, C20.1, C27.1, Driver L.20 (VCC), Driver R.20 (VCC), Encoder_L1.1, Encoder_L2.1, IMU.1, L1.2, PROG.3, R12.2, R13.1, R14.1, SD_Card.4 (VDD), U1.1 (VBAT), U1.16 (VDD), U1.32 (VDD), U1.48 (VDD), U1.64 (VDD), U3.2 (VO), U7.2 (3.3V)
+5V: C14.1, C15.1, GRUZIK3.0.1, GRUZIK3.0.2, U2.2 (VO), U3.3 (VI)
/HSE_IN: C8.2, U1.5 (PF0), X1.3
/HSE_OUT: C10.2, U1.6 (PF1), X1.1
/LSE_IN: C11.2, U1.3 (PC14), X2.2
/LSE_OUT: C12.2, U1.4 (PC15), X2.1
ADC_IN2: R4.1, R6.2, U1.13 (PA1)
BOOT0: BOOT.2 (B), U1.61 (PB8)
ENC_L_A: Encoder_L1.3, U1.45 (PA11)
ENC_L_B: Encoder_L1.4, U1.46 (PA12)
ENC_R_A: Encoder_L2.3, U1.9 (PC1)
ENC_R_B: Encoder_L2.4, U1.8 (PC0)
GND: +VIN-.2, BOOT.1 (A), C1.2, C2.2, C3.2, C4.2, C5.2, C6.2, C7.2, C8.1, C9.1, C10.1, C11.1, C12.1, C13.2, C14.2, C15.2, C16.2, C17.2, C18.2, C19.2, C20.2, C23.2, C24.2, C27.2, D1.1 (K), D2.1 (K), D3.1 (K), D6.1 (K), D7.1 (K), Driver L.3 (PGND1), Driver L.4 (PGND1), Driver L.9 (PGND2), Driver L.10 (PGND2), Driver L.18 (GND), Driver R.3 (PGND1), Driver R.4 (PGND1), Driver R.9 (PGND2), Driver R.10 (PGND2), Driver R.18 (GND), Encoder_L1.2, Encoder_L2.2, GRUZIK3.0.16, GRUZIK3.0.17, IMU.2, KEY.2 (B), PROG.5, PROG.7, R5.1, R6.1, RESET.1 (A), SD_Card.6 (VSS), SD_Card.9 (SHIELD), U1.15 (VSS), U1.27 (VSSA), U1.31 (VSS), U1.47 (VSS), U1.63 (VSS), U2.1 (GND), U3.1 (GND), U7.1 (GND), X1.2, X1.4
I2C3_IMU_INT: IMU.3, U1.39 (PC7)
I2C3_SCL: IMU.5, R14.2, U1.40 (PC8)
I2C3_SDA: IMU.4, R13.2, U1.41 (PC9)
LED_1: R3.2, U1.23 (PC5)
LED_2: R2.2, U1.22 (PC4)
LED_3: R1.2, U1.21 (PA7)
LED_4: R7.2, U1.20 (PA6)
LED_ON: GRUZIK3.0.15, U1.2 (PC13)
LPUART1_RX: U1.17 (PA3), U7.3 (Tx)
LPUART1_TX: U1.14 (PA2), U7.4 (Rx)
Motor_L_A: Driver L.17 (BIN1), Driver L.21 (AIN1), U1.42 (PA8)
Motor_L_B: Driver L.16 (BIN2), Driver L.22 (AIN2), U1.43 (PA9)
Motor_R_A: Driver R.17 (BIN1), Driver R.21 (AIN1), U1.10 (PC2)
Motor_R_B: Driver R.16 (BIN2), Driver R.22 (AIN2), U1.11 (PC3)
Motor_STBY: Driver L.19 (STBY), Driver R.19 (STBY), U1.38 (PC6)
NRST: C9.2, PROG.12, RESET.2 (B), U1.7 (PG10)
unnamed: D1.2 (A), R1.1
unnamed: D2.2 (A), R2.1
unnamed: D3.2 (A), R3.1
unnamed: D6.2 (A), R7.1
unnamed: D7.2 (A), R8.2
unnamed: KEY.1 (A), R11.2, R12.1
unnamed: Driver R.5 (AO2), Driver R.6 (AO2), Driver R.7 (BO2), Driver R.8 (BO2), P1.1
unnamed: Driver R.1 (AO1), Driver R.2 (AO1), Driver R.11 (BO1), Driver R.12 (BO1), P2.1
unnamed: Driver L.5 (AO2), Driver L.6 (AO2), Driver L.7 (BO2), Driver L.8 (BO2), P3.1
unnamed: Driver L.1 (AO1), Driver L.2 (AO1), Driver L.11 (BO1), Driver L.12 (BO1), P4.1
unnamed: PROG.11, R5.2
unnamed: R11.1, U7.12 (KEY)
unnamed: R8.1, U7.11 (LED)
PWM_L: Driver L.15 (PWMB), Driver L.23 (PWMA), U1.44 (PA10)
PWM_R: Driver R.15 (PWMB), Driver R.23 (PWMA), U1.12 (PA0)
SENSOR1: GRUZIK3.0.14, U1.62 (PB9)
SENSOR2: GRUZIK3.0.13, U1.60 (PB7)
SENSOR3: GRUZIK3.0.12, U1.59 (PB6)
SENSOR4: GRUZIK3.0.11, U1.58 (PB5)
SENSOR5: GRUZIK3.0.10, U1.57 (PB4)
SENSOR6: GRUZIK3.0.9, U1.55 (PD2)
SENSOR7: GRUZIK3.0.8, U1.54 (PC12)
SENSOR8: GRUZIK3.0.7, U1.53 (PC11)
SENSOR9: GRUZIK3.0.6, U1.52 (PC10)
SENSOR10: GRUZIK3.0.5, U1.51 (PA15)
SENSOR11: GRUZIK3.0.4, U1.18 (PA4)
SENSOR12: GRUZIK3.0.3, U1.19 (PA5)
SPI2_CLK: SD_Card.5 (CLK), U1.35 (PB13)
SPI2_CS: SD_Card.2 (DAT3/CD), U1.34 (PB12)
SPI2_MISO: SD_Card.7 (DAT0), U1.36 (PB14)
SPI2_MOSI: SD_Card.3 (CMD), U1.37 (PB15)
SYS_JTCK_SWCLK: PROG.6, U1.50 (PA14)
SYS_JTDO_SWO: PROG.8, U1.56 (PB3)
SYS_JTMS_SWDIO: PROG.4, U1.49 (PA13)
VDC: +VIN-.1, C13.1, C18.1, C19.1, C23.1, C24.1, Driver L.13 (VM2), Driver L.14 (VM3), Driver L.24 (VM1), Driver R.13 (VM2), Driver R.14 (VM3), Driver R.24 (VM1), R4.2, U2.3 (VI)
VREF+: C2.1, C3.1, L1.1, U1.28 (VREF+), U1.29 (VDDA)

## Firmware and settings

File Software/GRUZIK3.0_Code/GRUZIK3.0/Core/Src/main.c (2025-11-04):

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
/* Includes ------------------------------------------------------------------*/
#include "main.h"
#include "adc.h"
#include "dma.h"
#include "app_fatfs.h"
#include "i2c.h"
#include "usart.h"
#include "spi.h"
#include "tim.h"
#include "gpio.h"

/* USER CODE BEGIN Includes */
#include "stdlib.h"
#include "stdio.h"
#include "string.h"
#include "Line_Follower.h"
#include "RingBuffer.h"
#include "SimpleParser.h"
#include "motor.h"
#include "LowPassFilter.h"
#include "TJ_MPU6050.h"
#include "map.h"
/* USER CODE END Includes */


/* USER CODE BEGIN PV */
	/*Defines*/
//	#define true 1;
//	#define false 0;

	//uint8_t DrivingOnMap = 1;
	uint8_t SDReadingReady = 0;
	#define ENDLINE '\n'

	/*Sensor*/
	#define SENSOR_SCALE 1 // sensor values multiplier -- for tests only

	/*MAP*/
	#define CURVATURE_COMPENSATION 0
	Map_t map;
	/*FatFS variables*/
	FRESULT FatFsResult;
	FATFS SdFatFs;
	FIL SdCardFile;

	/*IMU*/
	#define YAW_MEASUREMENT_PERIOD 0.001f//s
	RawData_Def myAccelRaw, myGyroRaw;
	ScaledData_Def myAccelScaled, myGyroScaled;
	MPU_ConfigTypeDef myMpuConfig;

	float Yaw;
	float Orientation;

	/*Encoders*/
	#define PI_MOTOR_SPEED_REGULATION 1
	#define LOW_PASS_FILTER_ALPHA 0.7
	LineFollower_t GRUZIK;
	motor_t Motor_L;
	motor_t Motor_R;

	uint16_t timer_counter_L;
	uint16_t timer_counter_R;

	/*Rest of PIDR regulator*/
	int Sensors_read = 0x000000000000;
	int Position;
	float Ki = 0;
	float Kr = 0;
	int P, I, D, R;
	int Last_error = 0;
	int Errors[10] = {0,0,0,0,0,0,0,0,0,0};
	int Error_sum = 0;
	int Last_end = 0;	// 0 -> Left, 1 -> Right
	int Last_idle = 0;
	float Speed_level = 1;
	int ARR = 4;
	int actives = 0;
	uint32_t LastEndTimer;

	/*Communication*/
    char buffer[28];
    uint8_t buffer_2[60];
    uint8_t RxData;
	RingBuffer_t RB, ReceiveBuffer;
	uint8_t ReceivedData[32];
	uint8_t ReceivedLines;

/* USER CODE END PV */

void SystemClock_Config(void);
/* USER CODE BEGIN PFP */
void PID_control();
int errors_sum (int index, int abs);
void past_errors (int error);
void forward_brake(int pos_right, int pos_left);
int QTR8_read();
void sharp_turn();
void motor_control (double pos_right, double pos_left);
void Set_Pin_Input (GPIO_TypeDef *GPIOx, uint16_t GPIO_Pin);
void Set_Pin_Output (GPIO_TypeDef *GPIOx, uint16_t GPIO_Pin);
void delay_us (uint16_t us);
/* USER CODE END PFP */

/**
  * @brief  The application entry point.
  * @retval int
  */
int main(void)
{

  /* MCU Configuration--------------------------------------------------------*/

  /* Reset of all peripherals, Initializes the Flash interface and the Systick. */
  HAL_Init();

  /* Configure the system clock */
  SystemClock_Config();

  /* Initialize all configured peripherals */
  MX_GPIO_Init();
  MX_DMA_Init();
  MX_LPUART1_UART_Init();
  MX_ADC1_Init();
  MX_I2C3_Init();
  MX_SPI2_Init();
  MX_TIM1_Init();
  MX_TIM2_Init();
  MX_TIM4_Init();
  MX_TIM3_Init();
  MX_TIM5_Init();
  if (MX_FATFS_Init() != APP_OK) {
    Error_Handler();
  }
  /* USER CODE BEGIN 2 */
  	HAL_ADC_Start_DMA(&hadc1, (uint32_t*)&GRUZIK.Adc_Value, 1);

  	/*Initial values for driving on Optimized route*/
  	map.p = 0.13;//0.14
  	map.i = 0;
  	map.d = 13;//14

  	GRUZIK.DrivingOnMap = 1;


  	/*Set initial values for PID*/
    GRUZIK.Kp = 0.015;
  	GRUZIK.Kd = 0.085;
  	GRUZIK.Speed_offset = 0.014;

  	if(GRUZIK.DrivingOnMap)
  	{
		GRUZIK.Kp = map.p;
		GRUZIK.Kd = map.d;
		GRUZIK.Base_speed_R = map.i;
  	}

  	GRUZIK.Base_speed_R = 80;
  	GRUZIK.Base_speed_L = 80;
  	GRUZIK.Max_speed_R = 80;
  	GRUZIK.Max_speed_L = 80;

  	/*Sharp turn speed*/
  	GRUZIK.Sharp_bend_speed_right= -40;
  	GRUZIK.Sharp_bend_speed_left= 85;
  	GRUZIK.Bend_speed_right= -50;
  	GRUZIK.Bend_speed_left= 90;

  	map.Kk = 0;


    /*Start receiving data from Blue tooth*/
    HAL_UART_Receive_IT(&hlpuart1, &RxData, 1);

    /*encoders*/
    HAL_TIM_Base_Start_IT(&htim5);// 100
    HAL_TIM_Encoder_Start(&htim4, TIM_CHANNEL_ALL); // Left Encoder
    HAL_TIM_Encoder_Start(&htim1, TIM_CHANNEL_ALL); // Right Encoder

    //         Motor     KP    KI
    Motor_Init(&Motor_R, 0.1, 0.2);//0.1 0.2
    Motor_Init(&Motor_L, 0.1, 0.2);
    LowPassFilter_Init(&Motor_R.EncoderRpmFilter, LOW_PASS_FILTER_ALPHA);
    LowPassFilter_Init(&Motor_L.EncoderRpmFilter, LOW_PASS_FILTER_ALPHA);
    LowPassFilter_Init(&Motor_L.MetersPerSecondLPF, LOW_PASS_FILTER_ALPHA);
    LowPassFilter_Init(&Motor_R.MetersPerSecondLPF, LOW_PASS_FILTER_ALPHA);

    /*SD Card file initialization*/
    FatFsResult = f_mount(&SdFatFs, "", 1);
    if(GRUZIK.DrivingOnMap != 1)
    {
    	while(!SDReadingReady)
    	{
    		FatFsResult = f_open(&SdCardFile, "GRUZIK.txt", FA_WRITE|FA_OPEN_APPEND);
    		if(FatFsResult == FR_OK)
    		{
    			SDReadingReady = 1;
    		}
    	}
    }
    else
    {
    	while(!SDReadingReady)
    	{
    		FatFsResult = f_open(&SdCardFile, "map.txt", FA_READ);
    		if(FatFsResult == FR_OK)
    		{
    			SDReadingReady = 1;
    		}
    	}
    }
	/*Start timers and PWM on channels*/
	HAL_TIM_Base_Start_IT(&htim3);
	HAL_TIM_PWM_Start(&htim2, TIM_CHANNEL_1);//right pwm
	HAL_TIM_PWM_Start(&htim2, TIM_CHANNEL_4);//left pwm

	/*IMU initialization*/
	//1. Initialize the MPU6050 module and I2C
	MPU6050_Init(&hi2c3);

	//2. Configure parameters
	myMpuConfig.Accel_Full_Scale = AFS_SEL_16g;
	myMpuConfig.ClockSource = Internal_8MHz;
	myMpuConfig.CONFIG_DLPF = DLPF_184A_188G_Hz;
	myMpuConfig.Gyro_Full_Scale = FS_SEL_2000;
	myMpuConfig.Sleep_Mode_Bit = 0;  //1: sleep mode, 0: normal mode
	MPU6050_Config(&myMpuConfig);

    /*LED diodes initial set*/
    HAL_GPIO_WritePin(LED_4_GPIO_Port, LED_4_Pin, GPIO_PIN_SET);
    HAL_GPIO_WritePin(LED_3_GPIO_Port, LED_3_Pin, GPIO_PIN_SET);
    HAL_GPIO_WritePin(LED_2_GPIO_Port, LED_2_Pin, GPIO_PIN_SET);
    HAL_GPIO_WritePin(LED_1_GPIO_Port, LED_1_Pin, GPIO_PIN_SET);

  /* USER CODE END 2 */

  /* Infinite loop */
  /* USER CODE BEGIN WHILE */
  while (1)
  {
    /* USER CODE END WHILE */

    /* USER CODE BEGIN 3 */
	  if(GRUZIK.DrivingOnMap == 0)
	  {
		  PID_control();
	  }

  }
  /* USER CODE END 3 */
}

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
/* USER CODE BEGIN 4 */
/*Interrupts*/
void HAL_UART_RxCpltCallback(UART_HandleTypeDef *huart)
{
	if(huart->Instance == LPUART1)
	{
		if(RB_Write(&ReceiveBuffer, RxData) == RB_OK)
		{
			if(RxData == ENDLINE)
			{
				ReceivedLines++;
			}
		}
    	HAL_UART_Receive_IT(&hlpuart1,&RxData, 1);
	}
}
/*Encoders reading at 1KHz */
void HAL_TIM_PeriodElapsedCallback(TIM_HandleTypeDef *htim)
{
	if(htim->Instance == TIM5)
	{
		/*Get Encoder values*/
		Motor_L.EncoderValue = __HAL_TIM_GET_COUNTER(&htim4);
		Motor_R.EncoderValue = __HAL_TIM_GET_COUNTER(&htim1);
		/*Set central point for encoders again*/
		htim4.Instance->CNT = 20000;
		htim1.Instance->CNT = 20000;

	    Motor_CalculateSpeed(&Motor_R);
	    Motor_CalculateSpeed(&Motor_L);

	    /*integration of Gyroscope data for Z axis*/
	    MPU6050_Get_Accel_Scale(&myAccelScaled);
	    MPU6050_Get_Gyro_Scale(&myGyroScaled);

	    Orientation += map.OriIMU / 0.01745329251f;

		if(GRUZIK.blockinterrups == 0)
		{															   // 0.001
			if((GRUZIK.DrivingOnMap == 1)&&(SDReadingReady == 1))     // 0.0015
			{                                                         // 0.00095
			  map.OriIMU = (((myGyroScaled.z * YAW_MEASUREMENT_PERIOD) - 0.0015)* 0.01745329251f) * 1;//1.03325
			  DriveOnMap(&map, &Motor_L, &Motor_R);
			}
			else if((GRUZIK.DrivingOnMap == 0)&&(SDReadingReady == 1))// + 0.00200
			{                                                         // + 0.00125
			  map.OriIMU = (((myGyroScaled.z * YAW_MEASUREMENT_PERIOD) + 0.004)* 0.01745329251f) * 1.2705f;//1.3325 // zwiększenie zamyka trase
//			  MapUpdate(&map, &Motor_L, &Motor_R);                     //- 0.0065                    1.273

				//map.OriIMU = ((myGyroScaled.z * YAW_MEASUREMENT_PERIOD) - 0.001)* 0.01745329251f;
				MapUpdateV2(&map, &Motor_L, &Motor_R);
			}
		}

		  /*If there is a message form Bluetooth Parser it*/
		  if(ReceivedLines > 0)
		  {
			  Parser_TakeLine(&ReceiveBuffer, ReceivedData);
			  Parser_Parse(ReceivedData,&GRUZIK);

			  ReceivedLines--;
		  }
		  /*After one cycle of un-mapping drive slowly with route for 2s and then stop*/
		  if(GRUZIK.UnMappingDone == 1)
		  {
			  if(HAL_GetTick() >= (GRUZIK.DoneUnMappingTimer + 1750))
			  {
					HAL_GPIO_WritePin(GPIOC, GPIO_PIN_6, GPIO_PIN_RESET);
					HAL_GPIO_WritePin(GPIOC, GPIO_PIN_5, GPIO_PIN_RESET);
					HAL_GPIO_WritePin(GPIOA, GPIO_PIN_6, GPIO_PIN_RESET);
			  }
		  }
	}
}
/*Functions*/
void delay_us (uint16_t us) //Blocking function
{
	__HAL_TIM_SET_COUNTER(&htim3,0);  // set the counter value a 0
	while (__HAL_TIM_GET_COUNTER(&htim3) < us);  // wait for the counter to reach the us input in the parameter
}

void Set_Pin_Output (GPIO_TypeDef *GPIOx, uint16_t GPIO_Pin)
{
	GPIO_InitTypeDef GPIO_InitStruct = {0};
	GPIO_InitStruct.Pin = GPIO_Pin;
	GPIO_InitStruct.Mode = GPIO_MODE_OUTPUT_PP;
	GPIO_InitStruct.Speed = GPIO_SPEED_FREQ_LOW;
	HAL_GPIO_Init(GPIOx, &GPIO_InitStruct);
}

void Set_Pin_Input (GPIO_TypeDef *GPIOx, uint16_t GPIO_Pin)
{
	GPIO_InitTypeDef GPIO_InitStruct = {0};
	GPIO_InitStruct.Pin = GPIO_Pin;
	GPIO_InitStruct.Mode = GPIO_MODE_INPUT;
	GPIO_InitStruct.Pull = GPIO_PULLUP;
	HAL_GPIO_Init(GPIOx, &GPIO_InitStruct);
}


void motor_control (double pos_right, double pos_left)

{
	#ifdef PI_MOTOR_SPEED_REGULATION
	{
		if (pos_left < 0 )
		{
			Motor_L.set_speed = (pos_left * -1);
			PI_Loop(&Motor_L);

			__HAL_TIM_SET_COMPARE (&htim2, TIM_CHANNEL_4, (uint32_t)((ARR*Motor_L.speed) * GRUZIK.Speed_level));//PWM_L
			HAL_GPIO_WritePin(Motor_L_A_GPIO_Port, Motor_L_B_Pin, GPIO_PIN_SET);
			HAL_GPIO_WritePin(Motor_L_B_GPIO_Port, Motor_L_A_Pin, GPIO_PIN_RESET);

		}
		else
		{
			Motor_L.set_speed = pos_left;
			PI_Loop(&Motor_L);

			__HAL_TIM_SET_COMPARE (&htim2, TIM_CHANNEL_4, (uint32_t)((ARR*Motor_L.speed) * GRUZIK.Speed_level));//PWM_L
			HAL_GPIO_WritePin(Motor_L_A_GPIO_Port, Motor_L_B_Pin, GPIO_PIN_RESET);
			HAL_GPIO_WritePin(Motor_L_B_GPIO_Port, Motor_L_A_Pin, GPIO_PIN_SET);
		}
		if (pos_right < 0 )
		{
			Motor_R.set_speed = (pos_right * -1);
			PI_Loop(&Motor_R);

			__HAL_TIM_SET_COMPARE (&htim2, TIM_CHANNEL_1, (uint32_t)((ARR*Motor_R.speed) * GRUZIK.Speed_level));//PWM_R
			HAL_GPIO_WritePin(Motor_R_A_GPIO_Port, Motor_R_A_Pin, GPIO_PIN_SET);
			HAL_GPIO_WritePin(Motor_R_B_GPIO_Port, Motor_R_B_Pin, GPIO_PIN_RESET);
		}
		else
		{
			Motor_R.set_speed = pos_right;
			PI_Loop(&Motor_R);

			__HAL_TIM_SET_COMPARE (&htim2, TIM_CHANNEL_1, (uint32_t)((ARR*Motor_R.speed) * GRUZIK.Speed_level));//PWM_R
			HAL_GPIO_WritePin(Motor_R_A_GPIO_Port, Motor_R_A_Pin, GPIO_PIN_RESET);
			HAL_GPIO_WritePin(Motor_R_B_GPIO_Port, Motor_R_B_Pin, GPIO_PIN_SET);
		}
	}
	#else
	{
		if (pos_left < 0 )
		{
			__HAL_TIM_SET_COMPARE (&htim2, TIM_CHANNEL_4, (uint32_t)((ARR*pos_left*-1) * GRUZIK.Speed_level));//PWM_L
			HAL_GPIO_WritePin(Motor_L_A_GPIO_Port, Motor_L_B_Pin, GPIO_PIN_SET);
			HAL_GPIO_WritePin(Motor_L_B_GPIO_Port, Motor_L_A_Pin, GPIO_PIN_RESET);

		}
		else
		{
			__HAL_TIM_SET_COMPARE (&htim2, TIM_CHANNEL_4, (uint32_t)((ARR*pos_left) * GRUZIK.Speed_level));//PWM_L
			HAL_GPIO_WritePin(Motor_L_A_GPIO_Port, Motor_L_B_Pin, GPIO_PIN_RESET);
			HAL_GPIO_WritePin(Motor_L_B_GPIO_Port, Motor_L_A_Pin, GPIO_PIN_SET);
		}
		if (pos_right < 0 )
		{
			__HAL_TIM_SET_COMPARE (&htim2, TIM_CHANNEL_1, (uint32_t)((ARR*pos_right* -1) * GRUZIK.Speed_level));//PWM_R
			HAL_GPIO_WritePin(Motor_R_A_GPIO_Port, Motor_R_A_Pin, GPIO_PIN_SET);
			HAL_GPIO_WritePin(Motor_R_B_GPIO_Port, Motor_R_B_Pin, GPIO_PIN_RESET);
		}
		else
		{
			__HAL_TIM_SET_COMPARE (&htim2, TIM_CHANNEL_1, (uint32_t)((ARR*pos_right) * GRUZIK.Speed_level));//PWM_R
			HAL_GPIO_WritePin(Motor_R_A_GPIO_Port, Motor_R_A_Pin, GPIO_PIN_RESET);
			HAL_GPIO_WritePin(Motor_R_B_GPIO_Port, Motor_R_B_Pin, GPIO_PIN_SET);
		}
	}
	#endif

}


void sharp_turn ()
{

	if (Last_idle < 25)
	{
		if (Last_end == 1)
			motor_control(GRUZIK.Sharp_bend_speed_right, GRUZIK.Sharp_bend_speed_left);
		else
			motor_control(GRUZIK.Sharp_bend_speed_left, GRUZIK.Sharp_bend_speed_right);
	}
	else
	{
		if (Last_end == 1)
			motor_control(GRUZIK.Bend_speed_right, GRUZIK.Bend_speed_left);
		else
			motor_control(GRUZIK.Bend_speed_left, GRUZIK.Bend_speed_right);
	}
}
int QTR8_read ()
{
	HAL_GPIO_WritePin(LEDON_GPIO_Port, LEDON_Pin, 1);

	Set_Pin_Output(SENSOR1_GPIO_Port, SENSOR1_Pin);
	Set_Pin_Output(SENSOR2_GPIO_Port, SENSOR2_Pin);
	Set_Pin_Output(SENSOR3_GPIO_Port, SENSOR3_Pin);
	Set_Pin_Output(SENSOR4_GPIO_Port, SENSOR4_Pin);
	Set_Pin_Output(SENSOR5_GPIO_Port, SENSOR5_Pin);
	Set_Pin_Output(SENSOR6_GPIO_Port, SENSOR6_Pin);
	Set_Pin_Output(SENSOR7_GPIO_Port, SENSOR7_Pin);
	Set_Pin_Output(SENSOR8_GPIO_Port, SENSOR8_Pin);
	Set_Pin_Output(SENSOR9_GPIO_Port, SENSOR9_Pin);
	Set_Pin_Output(SENSOR10_GPIO_Port, SENSOR10_Pin);
	Set_Pin_Output(SENSOR11_GPIO_Port, SENSOR11_Pin);
	Set_Pin_Output(SENSOR12_GPIO_Port, SENSOR12_Pin);

	HAL_GPIO_WritePin (SENSOR1_GPIO_Port, SENSOR1_Pin, 1);
	HAL_GPIO_WritePin (SENSOR2_GPIO_Port, SENSOR2_Pin, 1);
	HAL_GPIO_WritePin (SENSOR3_GPIO_Port, SENSOR3_Pin, 1);
	HAL_GPIO_WritePin (SENSOR4_GPIO_Port, SENSOR4_Pin, 1);
	HAL_GPIO_WritePin (SENSOR5_GPIO_Port, SENSOR5_Pin, 1);
	HAL_GPIO_WritePin (SENSOR6_GPIO_Port, SENSOR6_Pin, 1);
	HAL_GPIO_WritePin (SENSOR7_GPIO_Port, SENSOR7_Pin, 1);
	HAL_GPIO_WritePin (SENSOR8_GPIO_Port, SENSOR8_Pin, 1);
	HAL_GPIO_WritePin (SENSOR9_GPIO_Port, SENSOR9_Pin, 1);
	HAL_GPIO_WritePin (SENSOR10_GPIO_Port, SENSOR10_Pin, 1);
	HAL_GPIO_WritePin (SENSOR11_GPIO_Port, SENSOR11_Pin, 1);
	HAL_GPIO_WritePin (SENSOR12_GPIO_Port, SENSOR12_Pin, 1);

	delay_us(10);

	Set_Pin_Input(SENSOR1_GPIO_Port, SENSOR1_Pin);
	Set_Pin_Input(SENSOR2_GPIO_Port, SENSOR2_Pin);
	Set_Pin_Input(SENSOR3_GPIO_Port, SENSOR3_Pin);
	Set_Pin_Input(SENSOR4_GPIO_Port, SENSOR4_Pin);
	Set_Pin_Input(SENSOR5_GPIO_Port, SENSOR5_Pin);
	Set_Pin_Input(SENSOR6_GPIO_Port, SENSOR6_Pin);
	Set_Pin_Input(SENSOR7_GPIO_Port, SENSOR7_Pin);
	Set_Pin_Input(SENSOR8_GPIO_Port, SENSOR8_Pin);
	Set_Pin_Input(SENSOR9_GPIO_Port, SENSOR9_Pin);
	Set_Pin_Input(SENSOR10_GPIO_Port, SENSOR10_Pin);
	Set_Pin_Input(SENSOR11_GPIO_Port, SENSOR11_Pin);
	Set_Pin_Input(SENSOR12_GPIO_Port, SENSOR12_Pin);

	// Threshold
	 delay_us(4500);
	 	 	 //!!! FOR SENSOR TESTING ONLY !!!//

//	 uint8_t sensory[12];
//	 sensory[0] = HAL_GPIO_ReadPin(SENSOR1_GPIO_Port, SENSOR1_Pin);
//	 sensory[1] = HAL_GPIO_ReadPin(SENSOR2_GPIO_Port, SENSOR2_Pin);
//	 sensory[2] = HAL_GPIO_ReadPin(SENSOR3_GPIO_Port, SENSOR3_Pin);
//	 sensory[3] = HAL_GPIO_ReadPin(SENSOR4_GPIO_Port, SENSOR4_Pin);
//	 sensory[4] = HAL_GPIO_ReadPin(SENSOR5_GPIO_Port, SENSOR5_Pin);
//	 sensory[5] = HAL_GPIO_ReadPin(SENSOR6_GPIO_Port, SENSOR6_Pin);
//	 sensory[6] = HAL_GPIO_ReadPin(SENSOR7_GPIO_Port, SENSOR7_Pin);
//	 sensory[7] = HAL_GPIO_ReadPin(SENSOR8_GPIO_Port, SENSOR8_Pin);
//	 sensory[8] = HAL_GPIO_ReadPin(SENSOR9_GPIO_Port, SENSOR9_Pin);
//	 sensory[9] = HAL_GPIO_ReadPin(SENSOR10_GPIO_Port, SENSOR10_Pin);
//	 sensory[10] = HAL_GPIO_ReadPin(SENSOR11_GPIO_Port, SENSOR11_Pin);
//	 sensory[11] = HAL_GPIO_ReadPin(SENSOR12_GPIO_Port, SENSOR12_Pin);
//	 uint8_t Message[124];
//	 sprintf((char*)Message,"S1: %d S2: %d S3: %d S4: %d S5: %d S6: %d S7: %d S8: %d S9: %d S10: %d S11: %d S12: %d \n\r", sensory[0],sensory[1],sensory[2],sensory[3],sensory[4],sensory[5],sensory[6],sensory[7],
//			 sensory[8],sensory[9],sensory[10],sensory[11]);
//	 HAL_UART_Transmit(&hlpuart1, Message, strlen((char*)Message), 100);

	Sensors_read = 0x000000000000;
	int pos = 0;
  int active = 0;

	if (HAL_GPIO_ReadPin(SENSOR1_GPIO_Port, SENSOR1_Pin)) { // LEFT SIDE
		Sensors_read |= 0x000000000001;
		pos += 1000 * SENSOR_SCALE;//1000
		active++;
		if(HAL_GetTick() > (LastEndTimer + 50))
		{
			LastEndTimer = HAL_GetTick();
			Last_end = 1;
		}

	}
	if (HAL_GPIO_ReadPin(SENSOR2_GPIO_Port, SENSOR2_Pin)) {
		Sensors_read |= 0x000000000010;
		pos += 2000 * SENSOR_SCALE;//2000
    active++;
    	//Last_end = 1;//1
  }
	if (HAL_GPIO_ReadPin(SENSOR3_GPIO_Port, SENSOR3_Pin)) {
		Sensors_read |= 0x000000000100;
		pos += 3000 * SENSOR_SCALE;//3000
    active++;
    	//Last_end = 1;//1
  }
	if (HAL_GPIO_ReadPin(SENSOR4_GPIO_Port, SENSOR4_Pin)) {
		Sensors_read |= 0x000000001000;
		pos += 4000 * SENSOR_SCALE;//4000
    active++;
  }
	if (HAL_GPIO_ReadPin(SENSOR5_GPIO_Port, SENSOR5_Pin)) {
		Sensors_read |= 0x000000010000;
		pos += 5000 * SENSOR_SCALE;//5000
    active++;
  }
	if (HAL_GPIO_ReadPin(SENSOR6_GPIO_Port, SENSOR6_Pin)) {
		Sensors_read |= 0x000000100000;
		pos += 6000 * SENSOR_SCALE;//6000
    active++;
  }
	if (HAL_GPIO_ReadPin(SENSOR7_GPIO_Port, SENSOR7_Pin)) {
		Sensors_read |= 0x000001000000;
		pos += 7000 * SENSOR_SCALE;//7000
    active++;
  }
	if (HAL_GPIO_ReadPin(SENSOR8_GPIO_Port, SENSOR8_Pin)) {
		Sensors_read |= 0x000010000000;
		pos += 8000 * SENSOR_SCALE;//8000
    active++;
  }
  if (HAL_GPIO_ReadPin(SENSOR9_GPIO_Port, SENSOR9_Pin)) {
	   Sensors_read |= 0x000100000000;
	   pos += 9000 * SENSOR_SCALE;//8000
	active++;

  }
  if (HAL_GPIO_ReadPin(SENSOR10_GPIO_Port, SENSOR10_Pin)) {
	   Sensors_read |= 0x001000000000;
	   pos += 10000 * SENSOR_SCALE;//8000
    active++;
	  // Last_end = 0;//0
  }
  if (HAL_GPIO_ReadPin(SENSOR11_GPIO_Port, SENSOR11_Pin)) {
	   Sensors_read |= 0x010000000000;
	   pos += 11000 * SENSOR_SCALE;//8000
    active++;
	  // Last_end = 0;//0
  }
  if (HAL_GPIO_ReadPin(SENSOR12_GPIO_Port, SENSOR12_Pin)) { // RIGHT SIDE
	   Sensors_read |= 0x100000000000;
	   pos += 12000 * SENSOR_SCALE;//8000
       active++;

        if(HAL_GetTick() > (LastEndTimer + 50))//50
		{
			LastEndTimer = HAL_GetTick();
			Last_end = 0;
		}

  }

  HAL_GPIO_WritePin(LEDON_GPIO_Port, LEDON_Pin, 0);

  actives = active;
	Position = pos/active;

	if (actives == 0)
		Last_idle++;
	else
		Last_idle = 0;

	return pos/active;
}


void forward_brake(int pos_right, int pos_left)
{
	if (actives == 0)
		sharp_turn();
	else
	  motor_control(pos_right, pos_left);
}

void past_errors (int error)
{
  for (int i = 9; i > 0; i--)
      Errors[i] = Errors[i-1];
  Errors[0] = error;
}

int errors_sum (int index, int abs)
{
  int sum = 0;
  for (int i = 0; i < index; i++)
  {
    if (abs == 1 && Errors[i] < 0)
      sum += -Errors[i];
    else
      sum += Errors[i];
  }
  return sum;
}

void PID_control()
{
  uint16_t position = QTR8_read();
  int error = (6500 * SENSOR_SCALE) - position;
  past_errors(error);

  P = error;
  GRUZIK.Error_P = P;
  I = errors_sum(5, 0);
  D = error - Last_error;
  GRUZIK.Error_D = D;
  R = errors_sum(5, 1);
  Last_error = error;

  int motorspeed = P*GRUZIK.Kp + I*Ki + D*GRUZIK.Kd;

  int motorspeedl = GRUZIK.Base_speed_L + motorspeed - R*Kr;
  int motorspeedr = GRUZIK.Base_speed_R - motorspeed - R*Kr;

  if (motorspeedl > GRUZIK.Max_speed_L)
    motorspeedl = GRUZIK.Max_speed_L;
  if (motorspeedr > GRUZIK.Max_speed_R)
    motorspeedr = GRUZIK.Max_speed_R;

	forward_brake(motorspeedr, motorspeedl);
}
/* USER CODE END 4 */
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


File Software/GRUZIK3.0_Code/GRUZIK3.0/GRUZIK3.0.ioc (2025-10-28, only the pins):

Mcu.UserName=STM32G474RETx
PA0.GPIO_Label=PWM_R
PA0.Signal=S_TIM2_CH1
PA1.Signal=ADC1_IN2
PA10.GPIO_Label=PWM_L
PA10.Signal=S_TIM2_CH4
PA11.GPIO_Label=ENCODER_L_1
PA11.Signal=S_TIM4_CH1
PA12.GPIO_Label=ENCODER_L_2
PA12.Signal=S_TIM4_CH2
PA13.GPIO_Label=T_SWDIO
PA13.Signal=SYS_JTMS-SWDIO
PA14.GPIO_Label=T_SWCLK
PA14.Signal=SYS_JTCK-SWCLK
PA15.GPIO_Label=SENSOR10
PA15.Signal=GPIO_Input
PA2.GPIO_Label=LPUART1_TX [STLINKV3E_VCP_RX]
PA2.Signal=LPUART1_TX
PA3.GPIO_Label=LPUART1_RX [STLINKV3E_VCP_TX]
PA3.Signal=LPUART1_RX
PA4.GPIO_Label=SENSOR11
PA4.Signal=GPIO_Input
PA5.GPIO_Label=SENSOR12
PA5.Signal=GPIO_Input
PA6.GPIO_Label=LED_4
PA6.Signal=GPIO_Output
PA7.GPIO_Label=LED_3
PA7.Signal=GPIO_Output
PA8.GPIO_Label=Motor_L_A
PA8.Signal=GPIO_Output
PA9.GPIO_Label=Motor_L_B
PA9.Signal=GPIO_Output
PB12.GPIO_Label=SPI2_CS
PB12.Signal=GPIO_Output
PB13.Signal=SPI2_SCK
PB14.Signal=SPI2_MISO
PB15.Signal=SPI2_MOSI
PB3.GPIO_Label=T_SWO
PB3.Signal=SYS_JTDO-SWO
PB4.GPIO_Label=SENSOR5
PB4.Signal=GPIO_Input
PB5.GPIO_Label=SENSOR4
PB5.Signal=GPIO_Input
PB6.GPIO_Label=SENSOR3
PB6.Signal=GPIO_Input
PB7.GPIO_Label=SENSOR2
PB7.Signal=GPIO_Input
PB9.GPIO_Label=SENSOR1
PB9.Signal=GPIO_Input
PC0.GPIO_Label=ENCODER_R_1
PC0.Signal=S_TIM1_CH1
PC1.GPIO_Label=ENCODER_R_2
PC1.Signal=S_TIM1_CH2
PC10.GPIO_Label=SENSOR9
PC10.Signal=GPIO_Input
PC11.GPIO_Label=SENSOR8
PC11.Signal=GPIO_Input
PC12.GPIO_Label=SENSOR7
PC12.Signal=GPIO_Input
PC13.GPIO_Label=LEDON
PC13.Signal=GPIO_Output
PC14-OSC32_IN.Signal=RCC_OSC32_IN
PC15-OSC32_OUT.Signal=RCC_OSC32_OUT
PC2.GPIO_Label=Motor_R_A
PC2.Signal=GPIO_Output
PC3.GPIO_Label=Motor_R_B
PC3.Signal=GPIO_Output
PC4.GPIO_Label=LED_2
PC4.Signal=GPIO_Output
PC5.GPIO_Label=LED_1
PC5.Signal=GPIO_Output
PC6.GPIO_Label=Motor_STBY
PC6.Signal=GPIO_Output
PC8.Signal=I2C3_SCL
PC9.Signal=I2C3_SDA
PD2.GPIO_Label=SENSOR6
PD2.Signal=GPIO_Input
PF0-OSC_IN.Signal=RCC_OSC_IN
PF1-OSC_OUT.Signal=RCC_OSC_OUT

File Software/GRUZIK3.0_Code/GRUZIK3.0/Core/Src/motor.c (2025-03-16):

/*
 * motor.c
 *
 *  Created on: 19 gru 2024
 *      Author: Szymon Nyderek
 */

#include "main.h"
#include "motor.h"
#include "LowPassFilter.h"
void Motor_CalculateSpeed(motor_t *motor)
{
	// (0.0) --  How many impulses did we get ?
	int impulses;
	impulses = (int32_t)motor->EncoderValue - 20000;

	// (0.1) -- Invert direction to " FORWARD "
	impulses = impulses * -1;

	/*Distance traveled in 0.001s (One cycle)*/

	motor->DistanceInMeasurement = ((float)impulses * WHEEL_CIRCUMFERENCE) / (IMPULSES_PER_ROTATION * GEAR_RATIO);
	/*Whole distance wheel has traveled*/
	motor->DistanceTraveled = motor->DistanceTraveled + motor->DistanceInMeasurement;

	/*Get meters per second*/
	/* m/s = m/ms * 1000 */
	motor->MetersPerSecond = motor->DistanceInMeasurement * -1000.0f; // 1s = 1000ms

	LowPassFilter_Update(&motor->MetersPerSecondLPF, motor->MetersPerSecond);

	motor->LpfDistanceInMeasurement = motor->MetersPerSecondLPF.output / -1000.0f;


    //How many times motor has rotated ?
	motor->NumberOfRotations = (float)impulses / 20000.0f;
	//Rotations per minute based on period and impulses
	motor->RPM = motor->NumberOfRotations * -60000.0f; //rotates per minute

	/*I know some of them are "magic values" other way it doesn't want to work*/

	if((motor->RPM >= 5000) || (motor->RPM <= -5000)) // |max| = 5000 Other readings are trash
	{
		motor->RPM = motor->PreviousRPM;
	}
	//Motor_SavePreviousRPMs(motor, motor->RPM);
	LowPassFilter_Update(&motor->EncoderRpmFilter, motor->RPM);
	motor->MetersPerHour = motor->EncoderRpmFilter.output / RPM_TO_MH;
	//motor->MetersPerHour = motor->RPM / RPM_TO_MH;
	motor->KilometersPerHour = motor->MetersPerHour / 1000;
	motor->MetersPerSecond = motor->MetersPerHour / 3600;
	motor->PreviousRPM = motor->EncoderRpmFilter.output;
}

void Motor_Init(motor_t *motor, float Kp, float Ki)
{
	motor->kp = Kp;
	motor->ki = Ki;
	motor->MetersPerSecondLPF.alpha = 0.1; // -- works like translation filter
}

void PI_Loop(motor_t *motor)
{
	motor->current_speed = motor->MetersPerSecond * 23; // From m/s to bananas per second //65

	//Get absolute speed
	if(motor->current_speed < 0)
	{
		motor->current_speed = motor->current_speed * -1;
		//Zastanów się czy faktycznie to jest potrzebne
	}

	//Get the difference between speed that we need and actual speed
	motor->error =  motor->set_speed - motor->current_speed;

	//Add current error to previous errors
	motor->Error_sum = motor->Error_sum +motor->P;
	if(motor->Error_sum > 100)
	{
		motor->Error_sum = 100;
	}
	else if(motor->Error_sum < -100)
	{
		motor->Error_sum = -100;
	}

	//Calculate new speed with PI parameters
	motor->speed = motor->set_speed + (motor->error * motor->kp) + (motor->Error_sum *motor->ki);

}

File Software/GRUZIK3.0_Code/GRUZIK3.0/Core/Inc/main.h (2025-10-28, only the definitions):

#define LEDON_Pin GPIO_PIN_13
#define LEDON_GPIO_Port GPIOC
#define ENCODER_R_1_Pin GPIO_PIN_0
#define ENCODER_R_1_GPIO_Port GPIOC
#define ENCODER_R_2_Pin GPIO_PIN_1
#define ENCODER_R_2_GPIO_Port GPIOC
#define Motor_R_A_Pin GPIO_PIN_2
#define Motor_R_A_GPIO_Port GPIOC
#define Motor_R_B_Pin GPIO_PIN_3
#define Motor_R_B_GPIO_Port GPIOC
#define PWM_R_Pin GPIO_PIN_0
#define PWM_R_GPIO_Port GPIOA
#define LPUART1_TX_Pin GPIO_PIN_2
#define LPUART1_TX_GPIO_Port GPIOA
#define LPUART1_RX_Pin GPIO_PIN_3
#define LPUART1_RX_GPIO_Port GPIOA
#define SENSOR11_Pin GPIO_PIN_4
#define SENSOR11_GPIO_Port GPIOA
#define SENSOR12_Pin GPIO_PIN_5
#define SENSOR12_GPIO_Port GPIOA
#define LED_4_Pin GPIO_PIN_6
#define LED_4_GPIO_Port GPIOA
#define LED_3_Pin GPIO_PIN_7
#define LED_3_GPIO_Port GPIOA
#define LED_2_Pin GPIO_PIN_4
#define LED_2_GPIO_Port GPIOC
#define LED_1_Pin GPIO_PIN_5
#define LED_1_GPIO_Port GPIOC
#define SPI2_CS_Pin GPIO_PIN_12
#define SPI2_CS_GPIO_Port GPIOB
#define Motor_STBY_Pin GPIO_PIN_6
#define Motor_STBY_GPIO_Port GPIOC
#define Motor_L_A_Pin GPIO_PIN_8
#define Motor_L_A_GPIO_Port GPIOA
#define Motor_L_B_Pin GPIO_PIN_9
#define Motor_L_B_GPIO_Port GPIOA
#define PWM_L_Pin GPIO_PIN_10
#define PWM_L_GPIO_Port GPIOA
#define ENCODER_L_1_Pin GPIO_PIN_11
#define ENCODER_L_1_GPIO_Port GPIOA
#define ENCODER_L_2_Pin GPIO_PIN_12
#define ENCODER_L_2_GPIO_Port GPIOA
#define T_SWDIO_Pin GPIO_PIN_13
#define T_SWDIO_GPIO_Port GPIOA
#define T_SWCLK_Pin GPIO_PIN_14
#define T_SWCLK_GPIO_Port GPIOA
#define SENSOR10_Pin GPIO_PIN_15
#define SENSOR10_GPIO_Port GPIOA
#define SENSOR9_Pin GPIO_PIN_10
#define SENSOR9_GPIO_Port GPIOC
#define SENSOR8_Pin GPIO_PIN_11
#define SENSOR8_GPIO_Port GPIOC
#define SENSOR7_Pin GPIO_PIN_12
#define SENSOR7_GPIO_Port GPIOC
#define SENSOR6_Pin GPIO_PIN_2
#define SENSOR6_GPIO_Port GPIOD
#define T_SWO_Pin GPIO_PIN_3
#define T_SWO_GPIO_Port GPIOB
#define SENSOR5_Pin GPIO_PIN_4
#define SENSOR5_GPIO_Port GPIOB
#define SENSOR4_Pin GPIO_PIN_5
#define SENSOR4_GPIO_Port GPIOB
#define SENSOR3_Pin GPIO_PIN_6
#define SENSOR3_GPIO_Port GPIOB
#define SENSOR2_Pin GPIO_PIN_7
#define SENSOR2_GPIO_Port GPIOB
#define SENSOR1_Pin GPIO_PIN_9
#define SENSOR1_GPIO_Port GPIOB

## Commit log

2025-02-24 Encoders Added
    [Connector.3mf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]
2025-03-03 Encoders Fixed :)
    PI motor speed controllers finally work as intended
    [GRUZIK3.0.ioc, SimpleParser.c, motor.h]
2025-03-16 Maping with Encoders done
2025-03-26 New motors and modes
    [Main_PCB_GRUZIK_3.0.kicad_sch]

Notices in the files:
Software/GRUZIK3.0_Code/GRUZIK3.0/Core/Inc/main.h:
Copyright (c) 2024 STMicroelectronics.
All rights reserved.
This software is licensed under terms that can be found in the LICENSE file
